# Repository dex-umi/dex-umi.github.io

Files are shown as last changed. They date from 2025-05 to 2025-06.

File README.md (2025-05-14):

# Academic Project Page Template
This is an academic paper project page template.

Example project pages built using this template are:
- https://horwitz.ai/probex
- https://vision.huji.ac.il/probegen
- https://horwitz.ai/mother
- https://horwitz.ai/spectral_detuning
- https://vision.huji.ac.il/ladeda
- https://vision.huji.ac.il/dsire
- https://horwitz.ai/podd
- https://dreamix-video-editing.github.io
- https://horwitz.ai/conffusion
- https://horwitz.ai/3d_ads/
- https://vision.huji.ac.il/ssrl_ad
- https://vision.huji.ac.il/deepsim

## Start using the template
To start using the template click on `Use this Template`.

The template uses html for controlling the content and css for controlling the style. 
To edit the websites contents edit the `index.html` file. It contains different HTML "building blocks", use whichever ones you need and comment out the rest.  

**IMPORTANT!** Make sure to replace the `favicon.ico` under `static/images/` with one of your own, otherwise your favicon is going to be a dreambooth image of me.

## Components
- Teaser video
- Images Carousel
- Youtube embedding
- Video Carousel
- PDF Poster
- Bibtex citation

## Tips:
- The `index.html` file contains comments instructing you what to replace, you should follow these comments.
- The `meta` tags in the `index.html` file are used to provide metadata about your paper 
(e.g. helping search engine index the website, showing a preview image when sharing the website, etc.)
- The resolution of images and videos can usually be around 1920-2048, there rarely a need for better resolution that take longer to load. 
- All the images and videos you use should be compressed to allow for fast loading of the website (and thus better indexing by search engines). For images, you can use [TinyPNG](https://tinypng.com), for videos you can need to find the tradeoff between size and quality.
- When using large video files (larger than 10MB), it's better to use youtube for hosting the video as serving the video from the website can take time.
- Using a tracker can help you analyze the traffic and see where users came from. [statcounter](https://statcounter.com) is a free, easy to use tracker that takes under 5 minutes to set up. 
- This project page can also be made into a github pages website.
- Replace the favicon to one of your choosing (the default one is of the Hebrew University). 
- Suggestions, improvements and comments are welcome, simply open an issue or contact me. You can find my contact information at [https://horwitz.ai](https://horwitz.ai)

## Acknowledgments
Parts of this project page were adopted from the [Nerfies](https://nerfies.github.io/) page.

## Website License
<br />This work is licensed under a <a rel="license" href="http://creativecommons.org/licenses/by-sa/4.0/">Creative Commons Attribution-ShareAlike 4.0 International License</a>.

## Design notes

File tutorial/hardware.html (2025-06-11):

Back to Main Page

# DexUMI Hardware Assembly Tutorial

## Step-by-step guide for building your DexUMI exoskeleton

## Exoskeleton Model Preview

Explore the CAD views of both XHand and Inspire Hand DexUMI

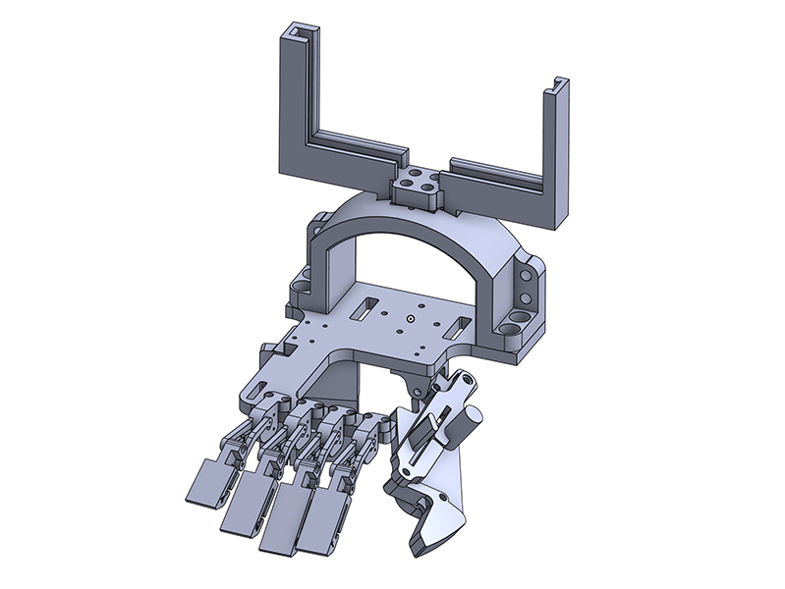
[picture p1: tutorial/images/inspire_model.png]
Inspire Hand DexUMI Model Preview
 (https://cad.onshape.com/documents/7e158032a91b5681734a0bac/w/ddb7f35eb14f420c872ab185/e/6841f3fc3ef2e646e71b0ba4)

Inspire Hand DexUMI Model

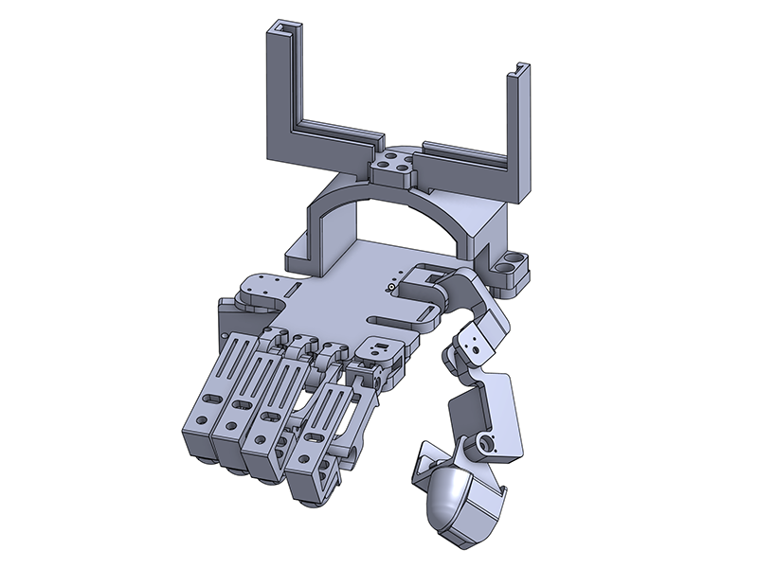
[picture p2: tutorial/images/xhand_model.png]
XHand DexUMI Model Preview
 (https://cad.onshape.com/documents/e4e375a7acd566624676e79d/w/0ad885893abcd26f135bcb35/e/56bcc60d6cd295dfe515c23f)

XHand DexUMI Model

Click on a model to view it directly in Onshape. You can also export the model in various 3D formats supported by Onshape.

- Download Formats: STL, STEP, SolidWorks, and more
- Printer: Bambu X1C
- Material: PLA-CF
- Print Settings: 50% sparse infill density, 50% infill/wall overlap, 10 wall loops

Download DexUMI_Inspire.3mf Download DexUMI_XHand.3mf

Feel free to tweak the settings based on your printer and material availability!

## PCB Sourcing

Information for sourcing and fabricating DexUMI circuit boards

Download Schematics Download Gerber Files Download Pick and Place Download BOM

### Step-by-step Tutorial of Ordering PCBA

To get started, you’ll first need to order the DexUMI circuit board. In this tutorial, we use JLCPCB as the PCB manufacturer.
On the JLCPCB homepage (https://jlcpcb.com/), click the Order Now button and follow the step-by-step guide in the image tutorial below.

First, upload the Gerber file we provided (click the download button above to get it).

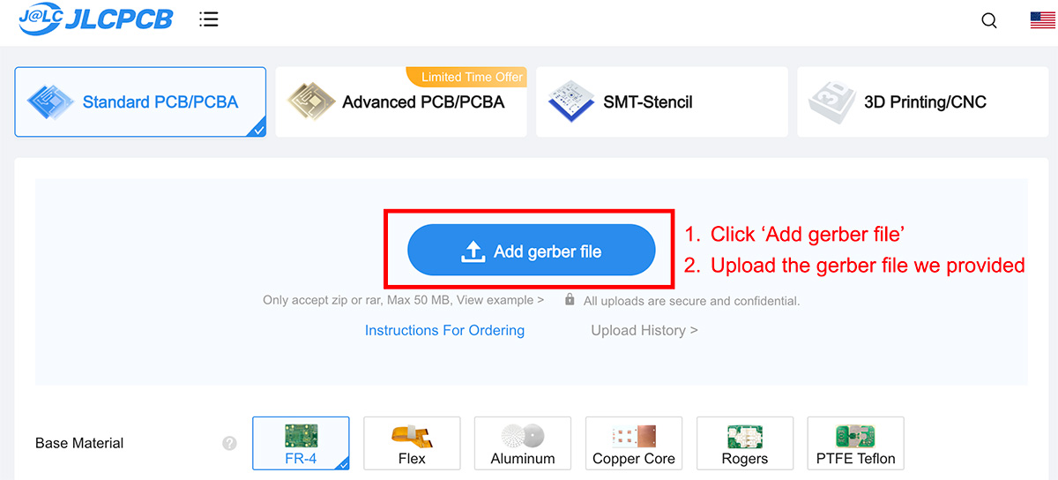
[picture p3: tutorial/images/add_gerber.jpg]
Add Gerber File


Second, follow the image tutorial below to select the correct manufacturer parameters.

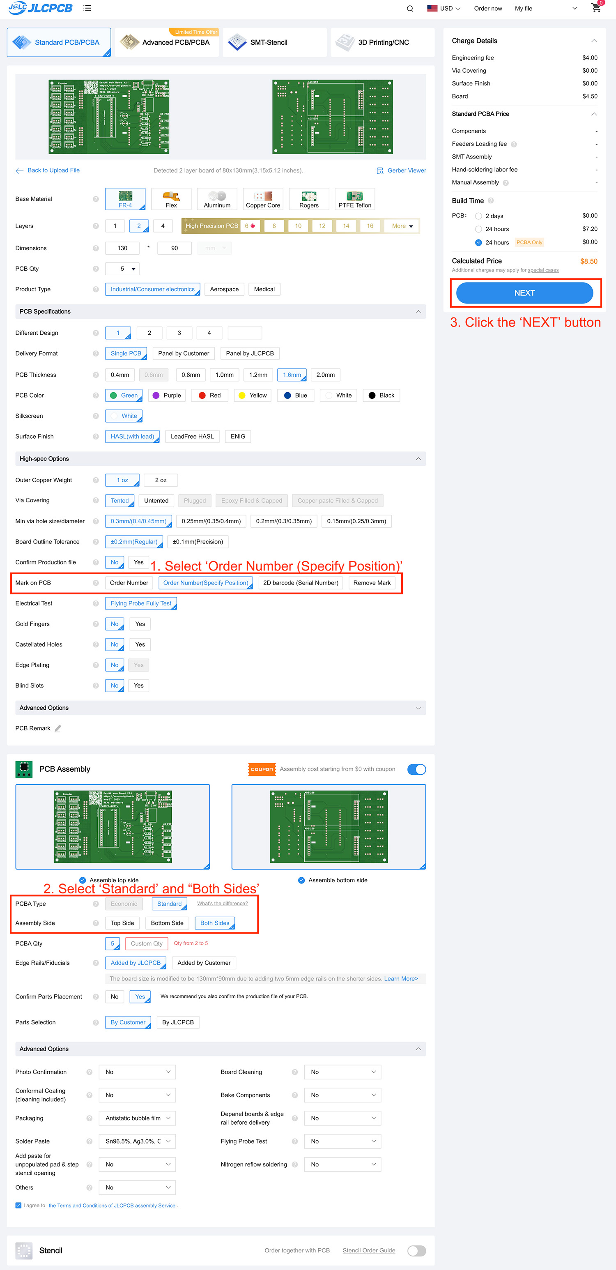
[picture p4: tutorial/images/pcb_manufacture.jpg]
PCB Manufacture Settings


On the new page, click the Bill of Materials column, then upload the BOM file and Pick and Place file we provided.

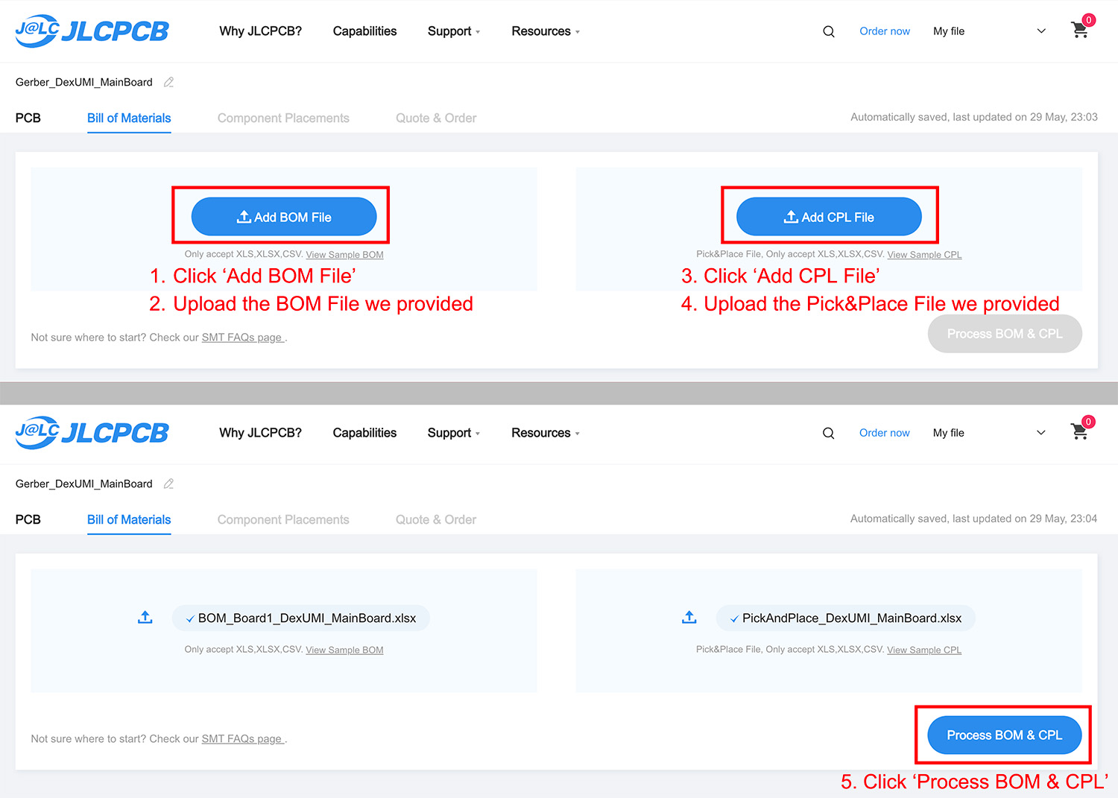
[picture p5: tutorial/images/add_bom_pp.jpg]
Add BOM and Pick and Place


After processing, you’ll be presented with a parts confirmation list. If everything is in stock, simply click the NEXT button. If not, you’ll need to manually select similar parts using the suggestions provided by the ordering system.

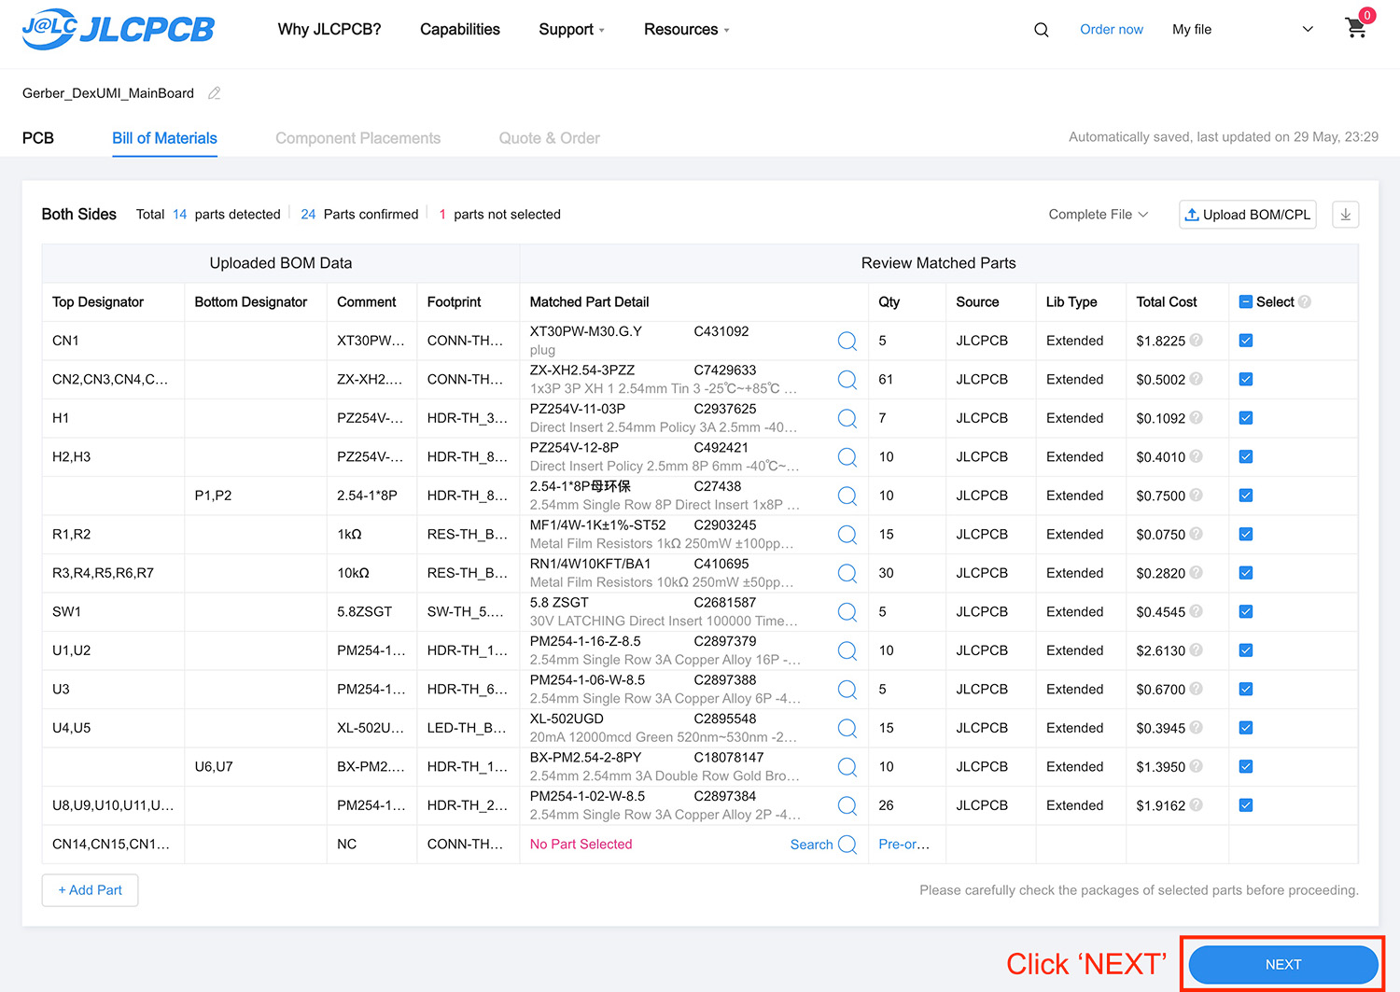
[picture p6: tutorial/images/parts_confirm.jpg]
Parts Confirmation


The system may display a message like Project has unselected parts. Don’t worry — this happens because we include some NC (Not Connected) parts, which are not meant to be assembled. Simply click the Do not place button to proceed.

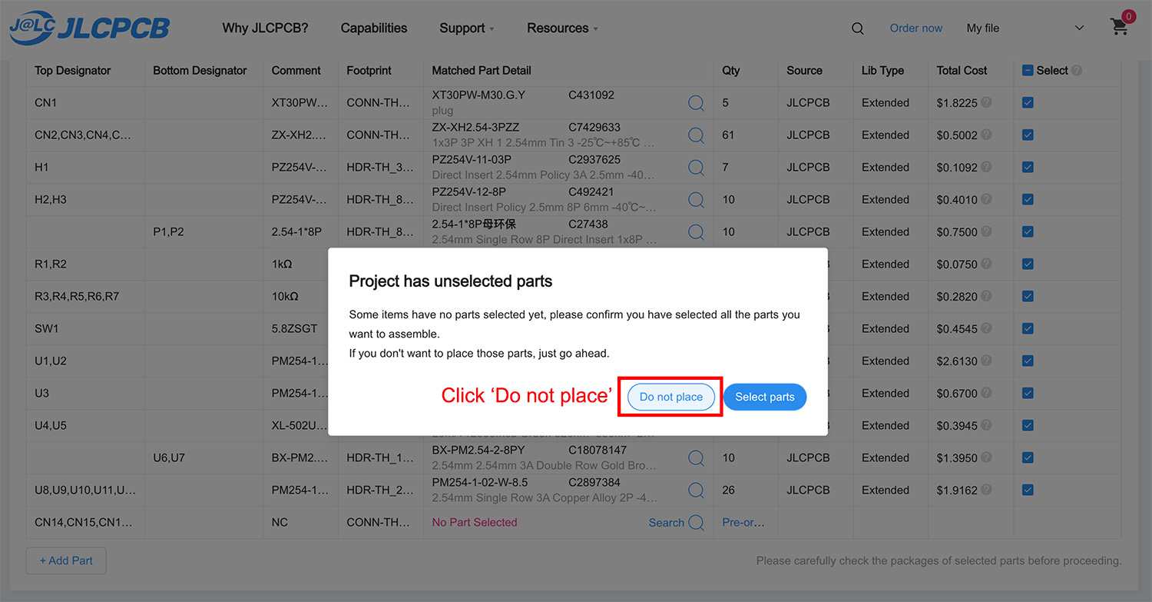
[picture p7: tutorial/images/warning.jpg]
Unselected Parts Warning


🎉 Hurray! The last step! You can now preview the 3D model of your circuit board. If all parts are rendered correctly and look similar to the images below, go ahead and click the NEXT button to place the order!

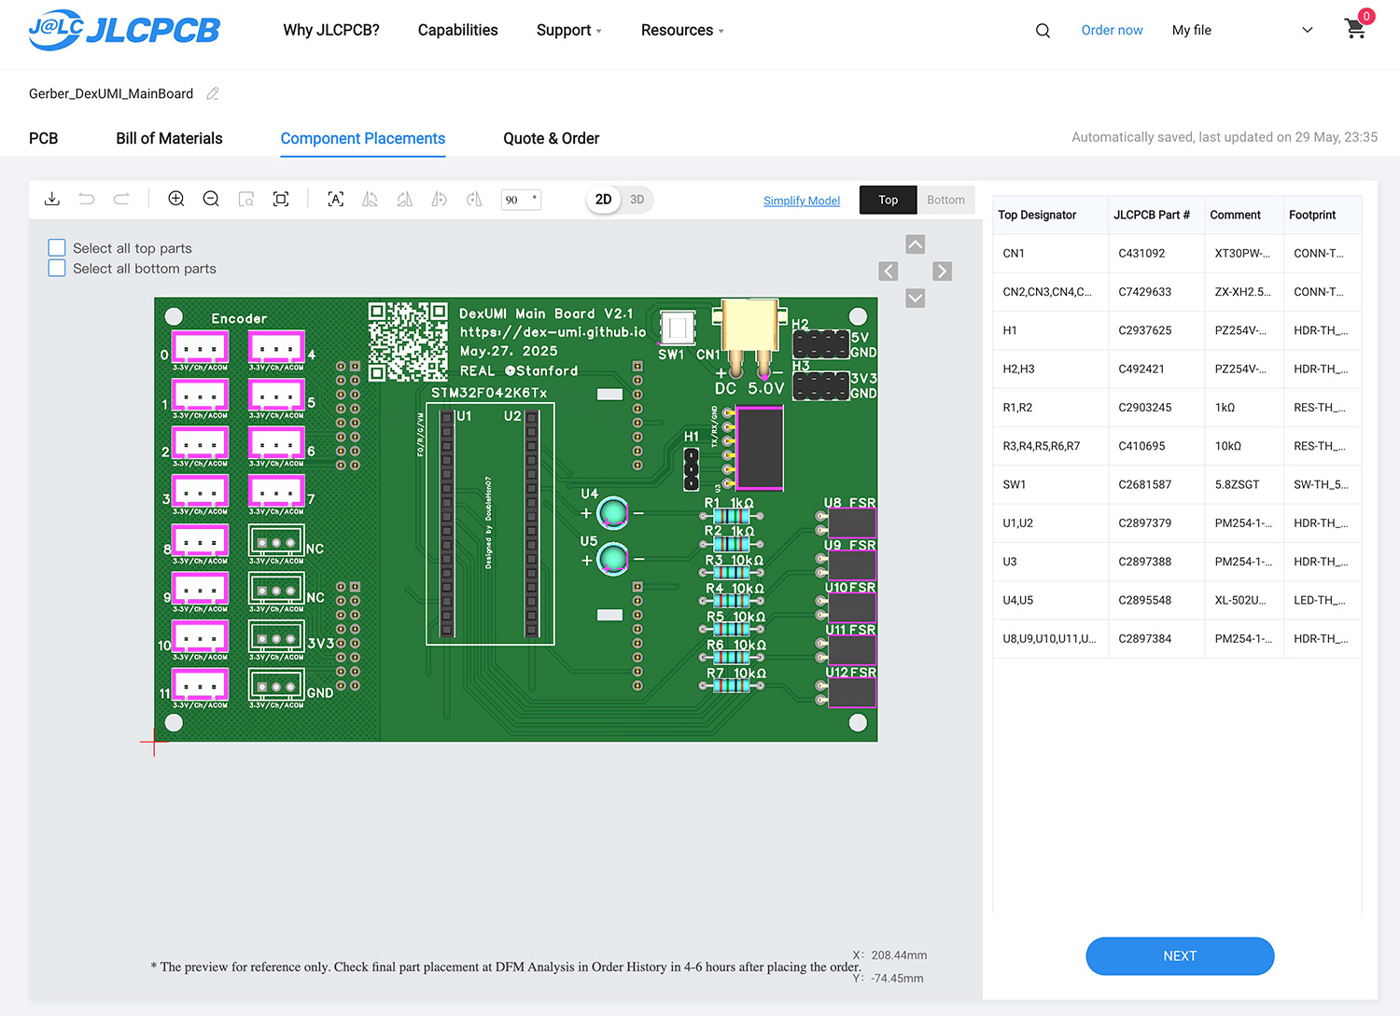
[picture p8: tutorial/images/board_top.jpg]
Board Top View


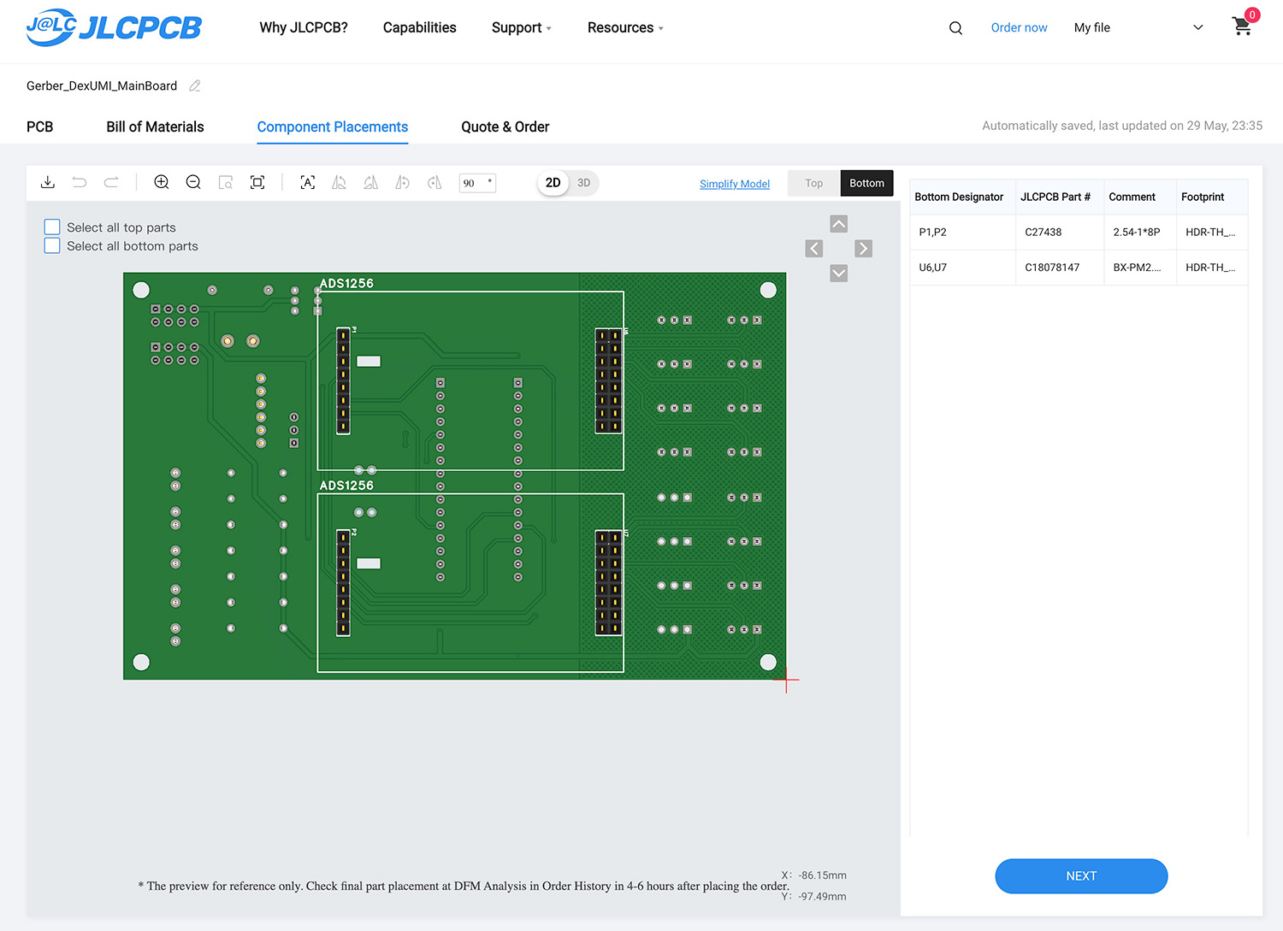
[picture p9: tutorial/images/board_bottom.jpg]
Board Bottom View


## Structural Bill of Materials (BOM)

All structural parts needed to build Inspire Hand and XHand DexUMI

This is a compact summary of all hardware components required. Tables are grouped by device and category. Click the links to purchase directly.

### Inspire Hand DexUMI

Part | Qty | Price
Materials
Bambu PLA-CF Matcha Green (https://us.store.bambulab.com/products/pla-cf?id=41158283591816) | 400g | $34.99 (1kg)
Electronics
XH 2.54mm-3P Wire 50cm (https://www.amazon.com/Kidisoii-2-54mm-Housing-Pre-Crimped-Adapter/dp/B0BW69ZB3M/) | 6 | $7.65 (5pcs)
RDC506018A Encoder: DigiKey (https://www.digikey.com/en/products/detail/alps-alpine/RDC506018A/19529120), Mouser (https://www.mouser.com/ProductDetail/Alps-Alpine/RDC506018A?qs=j%252B1pi9TdxUZl0Obrq5eEAQ%3D%3D) | 6 | $1.66 (1pc)
Fasteners
M1x8mm Screws (https://www.amazon.com/dp/B0C1SBGGY6/) | 4 | $7.99 (100pcs)
M1 Hex Nuts (https://www.mcmaster.com/90591A311/) | 4 | $4.47 (10pcs)
M2 Screws (6/12/16mm) (https://www.amazon.com/Kadrick-Assortment-Button-Stainless-Washers/dp/B0BX96SMW4/) | 8+1+2 | $8.99 (660pcs kit)
M2 Lock Nuts (https://www.amazon.com/binifiMux-100pcs-Stainless-Nylock-Locking/dp/B07L2W3QX3/) | 11 | $9.99 (100pcs)
M3 Lock Nuts (https://www.amazon.com/M3-Locknuts-Self-Lock-Stainless-Self/dp/B0D146SHYF/) | 4 | $5.99 (120pcs)
D-shape Screws
M3 Shoulder Screws 8mm (https://www.mcmaster.com/90265A119/) | 4 | $5.29 (1pc)
M3 Shoulder Screws 15mm (https://www.mcmaster.com/90265A182/) | 1 | $4.33 (1pc)
M3 Shoulder Screws 25mm (https://www.mcmaster.com/90265A874/) | 1 | $4.94 (1pc)
Accessories
Finger Sleeves (https://www.amazon.com/ELANE-Holster-Support-Elastic-basketball/dp/B08RYPTS54/) | 10 | $9.97 (40pcs)
3M TB641 Gripping Material (https://www.amazon.com/gp/product/B0093CQPW8/) | 1.5ft | $54.14 (15 ft)
iPhone Mounting
M3x16mm Screws + M3 Hex Nuts (https://www.amazon.com/Screws-Assortment-Plated-Socket-Washers/dp/B0D3X5CT2J/) | 4+4 | $8.99 (600pcs kit)
M6x20mm Screws + M6 Hex Nuts (https://www.amazon.com/Screws-Assortment-Stainless-Socket-Washers/dp/B0DFWMGFDM/) | 4+4 | $8.99 (172pcs kit)
Camera System
OAK-1 W (https://shop.luxonis.com/products/oak-1-w?variant=44051403604191) | 1 | $249 (1pc)
M4x6mm Screws (https://www.amazon.com/Kadrick-Assortment-Stainless-Washers-Wrenche/dp/B0BZ6Y8KRD/) | 2 | $9.99 (300pcs kit)
USB-C to USB-A (10ft) (https://www.amazon.com/Anker-Powerline-Pull-up-Resistor-MacBook/dp/B01MZIPYPY) | 1 | $16.99 (1pc)
Consumables
Loctite Threadlocker 242 (https://www.amazon.com/Loctite-Heavy-Duty-Threadlocker-Single/dp/B000I1RSNS/) | 0.03 fl oz | $5.98 (0.2 fl oz)
UV Resin (https://www.amazon.com/dp/B0BJ65T85R/) | 20g | $11.99 (30g)
Super Glue (https://www.amazon.com/Scotch-Super-Liquid-Ounces-AD114/dp/B001PILFVY/) | 1pc | $6.98 (4pcs)
Lubricate Grease (https://www.amazon.com/Lucas-Oil-10533-Lithium-Grease/dp/B004X70LZA/) | 0.2oz | $5.98 (8oz)

### XHand DexUMI

Part | Qty | Price
Materials
Bambu PLA-CF Matcha Green (https://us.store.bambulab.com/products/pla-cf?id=41158283591816) | 600g | $34.99 (1kg)
Electronics
XH 2.54mm-3P Wire 50cm (https://www.amazon.com/Kidisoii-2-54mm-Housing-Pre-Crimped-Adapter/dp/B0BW69ZB3M/) | 12 | $7.65 (5pcs)
RDC506018A Encoder: DigiKey (https://www.digikey.com/en/products/detail/alps-alpine/RDC506018A/19529120), Mouser (https://www.mouser.com/ProductDetail/Alps-Alpine/RDC506018A?qs=j%252B1pi9TdxUZl0Obrq5eEAQ%3D%3D) | 12 | $1.66 (1pc)
Fasteners
M2 Screws (12/16mm), M2 Hex Nuts (https://www.amazon.com/Kadrick-Assortment-Button-Stainless-Washers/dp/B0BX96SMW4/) | 7+6+8 | $8.99 (660pcs kit)
M2 Lock Nuts (https://www.amazon.com/binifiMux-100pcs-Stainless-Nylock-Locking/dp/B07L2W3QX3/) | 5 | $9.99 (100pcs)
M3 Hex Nuts (https://www.amazon.com/Screws-Assortment-Plated-Socket-Washers/dp/B0D3X5CT2J/) | 7 | $8.99 (600pcs kit)
M3 Lock Nuts (https://www.amazon.com/M3-Locknuts-Self-Lock-Stainless-Self/dp/B0D146SHYF/) | 7 | $5.99 (120pcs)
D-shape Screws
M3 Shoulder Screws 10mm (https://www.mcmaster.com/90265A121) | 9 | $3.12 (1pc)
M3 Shoulder Screws 20mm (https://www.mcmaster.com/90265A124) | 3 | $5.65 (1pc)
Accessories
Cable Ties (https://www.amazon.com/Reusable-Newlan-Adjustable-Organizer-Management/dp/B081HH5X61/) | 5 | $6.28 (60pcs)
3M TB641 Gripping Material (https://www.amazon.com/gp/product/B0093CQPW8/) | 1.5ft | $54.14 (15 ft)
iPhone Mounting
M3x16mm Screws + M3 Hex Nuts (https://www.amazon.com/Screws-Assortment-Plated-Socket-Washers/dp/B0D3X5CT2J/) | 4+4 | same as above
M6x20mm Screws + M6 Hex Nuts (https://www.amazon.com/Screws-Assortment-Stainless-Socket-Washers/dp/B0DFWMGFDM/) | 4+4 | $8.99 (172pcs kit)
Camera System
OAK-1 W (https://shop.luxonis.com/products/oak-1-w?variant=44051403604191) | 1 | $249 (1pc)
M4x6mm Screws (https://www.amazon.com/Kadrick-Assortment-Stainless-Washers-Wrenche/dp/B0BZ6Y8KRD/) | 2 | $9.99 (300pcs kit)
USB-C to USB-A (10ft) (https://www.amazon.com/Anker-Powerline-Pull-up-Resistor-MacBook/dp/B01MZIPYPY) | 1 | $16.99 (1pc)
Consumables
Loctite Threadlocker 242 (https://www.amazon.com/Loctite-Heavy-Duty-Threadlocker-Single/dp/B000I1RSNS/) | 0.02 fl oz | $5.98 (0.2 fl oz)
UV Resin (https://www.amazon.com/dp/B0BJ65T85R/) | 20g | $11.99 (30g)
Super Glue (https://www.amazon.com/Scotch-Super-Liquid-Ounces-AD114/dp/B001PILFVY/) | 1pc | $6.98 (4pcs)
Lubricate Grease (https://www.amazon.com/Lucas-Oil-10533-Lithium-Grease/dp/B004X70LZA/) | 0.2oz | $5.98 (8oz)

## Electronics Bill of Materials (BOM)

All electronic components and modules for DexUMI circuits

This is a compact summary of all hardware components required. Tables are grouped by device and category. Click the links to purchase directly.

### Electronic Modules

Part | Qty | Price
Modules
STM32F042K6T6 Core Board (https://www.aliexpress.com/i/2255800720094040.html) | 1 | $15.39 (1pc)
ADS1256 Module (https://www.aliexpress.us/item/3256806212460099.html) | 2 | $15.44 (1pc)
USB to TTL Module (https://www.amazon.com/JESSINIE-Module-CH343-Communication-Microcontroller/dp/B0D6352BS9/) | 1 | $9.95 (3pcs)
ST-Link V2 Downloader (https://www.amazon.com/AITRIP-Emulator-Downloader-Programmer-STM32F103C8T6/dp/B0D22S8WVX/) | 1 | $5.99 (1pc)
Accessories
DC Power Supply (https://www.amazon.com/ALIENTEK-Adjustable-DP100-Precision-Regulated/dp/B0CRDJBPRV/) | 1 | $60.15 (1pc)
XT30 Female Connectors w/ Wire (https://www.amazon.com/BDHI-Female-Connectors-Turnigy-BDHI-19/dp/B08FRBJL1C/) | 1 | $8.58 (5pcs)
Dupont Cable Male to Female (https://www.amazon.com/EDGELEC-Breadboard-1pin-1pin-Connector-Multicolored/dp/B07GD2BWPY/) | 3 | $6.98 (120pcs assorted)
Automotive Cloth Tape (https://www.amazon.com/Radio-Wiring-Harness-Cloth-Tape/dp/B08RS5P3WZ/) | 1 rolls | $9.99 (2pcs)

## Prepare Common Components

Essential components needed for both exoskeleton

#### Items

- D-screw components (screws, nuts, and tools)
- Encoder cable materials
- Encoder module parts

#### Make D-Screw

#### Prepare Encoder Cable

#### Build Encoder Module

## XHand Exoskeleton Assembly Guide

#### XHand Index Assembly Guide

#### XHand Middle/Ring/Pinky Assembly Guide

#### Xhand Thumb Assembly Guide

#### Assemble Fingers to the Palm

#### Oak Camera Mounting

#### Connect XHand Exoskeleton to the DexUMI Circuit Board

Follow the wiring sequence shown in the image below to connect encoders to the circuit board.

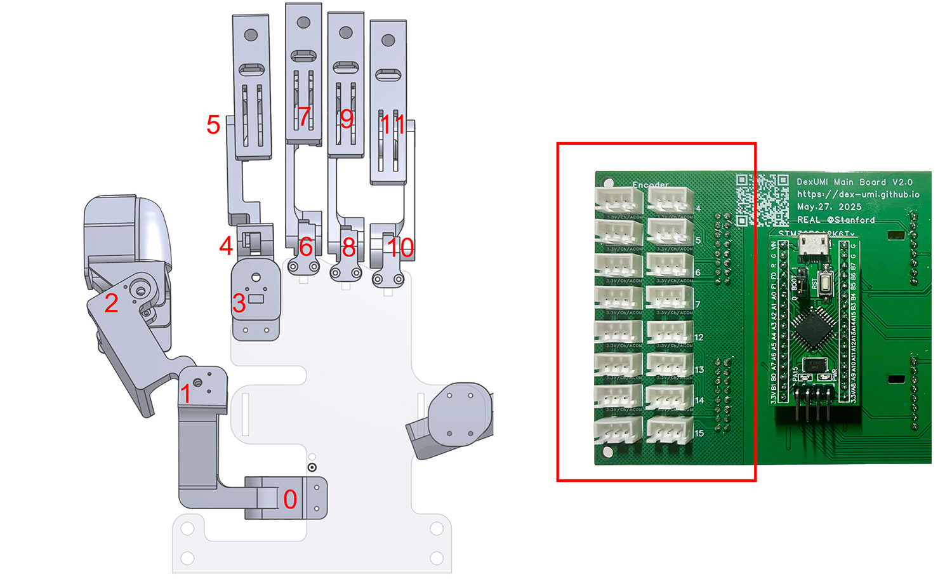
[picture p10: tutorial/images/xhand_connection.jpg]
XHand Connection Diagram


## Inspire Hand Exoskeleton Assembly

#### Inspire Index/Middle/Ring/Pinky Assembly Guide

#### Inspire Thumb Assembly Guide

#### Step 3: Oak Camera Mounting

#### Connect Inspire Hand Exoskeleton to the DexUMI Circuit Board

Follow the wiring sequence shown in the image below to connect encoders to the circuit board.

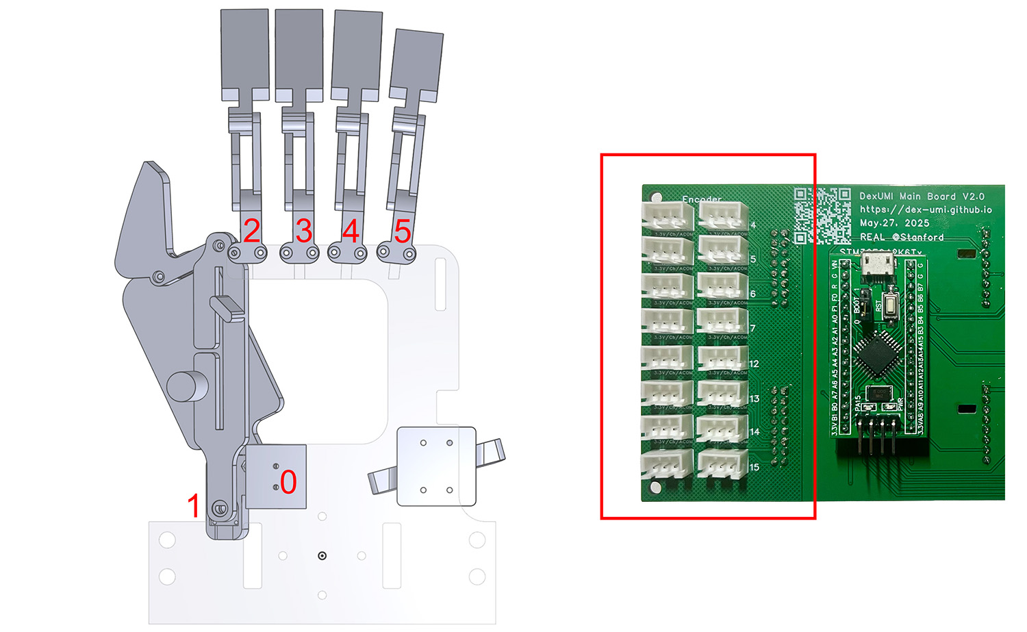
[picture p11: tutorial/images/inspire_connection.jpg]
Inspire Hand Connection Diagram


## Share Steps

Steps needed for both exoskeleton

#### iPhone Mounting

#### Finger Grip Tape

#### Flash the Firmware to DexUMI MCU

DexUMI Inspire Firmware (https://github.com/real-stanford/DexUMI/blob/main/embedded_system/assets/DexUMI_Inspire.hex) DexUMI XHand Firmware (https://github.com/real-stanford/DexUMI/blob/main/embedded_system/assets/DexUMI_XHand.hex)

To flash the firmware into the MCU, we first need to install openocd (https://openocd.org/pages/getting-openocd.html) on the target PC:

sudo apt-get install openocd

Then connect the MCU with ST-LINK V2, as shown below:

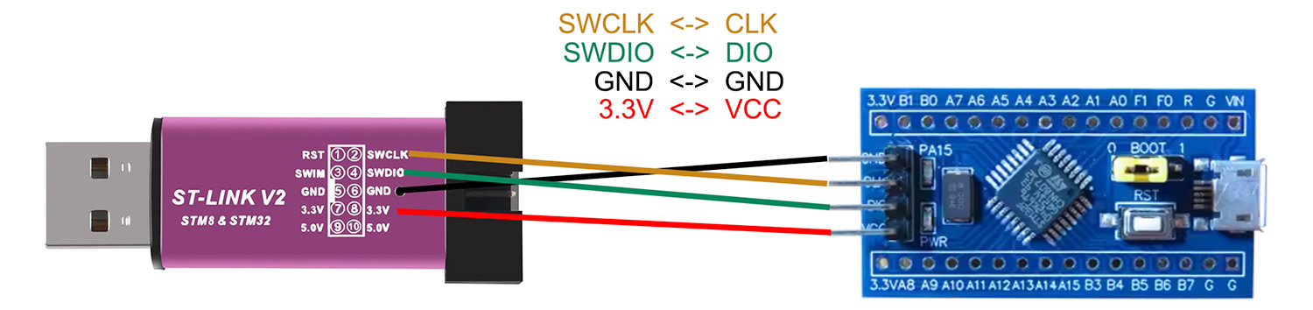
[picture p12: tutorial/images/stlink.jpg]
ST-LINK Connection Diagram


Finally, run this script to flash the firmware into the MCU.

For Inspire Hand DexUMI:

openocd -f interface/stlink-v2.cfg -f target/stm32f0x.cfg -c "program DexUMI_Inspire.hex verify reset exit"

For XHand DexUMI:

openocd -f interface/stlink-v2.cfg -f target/stm32f0x.cfg -c "program DexUMI_XHand.hex verify reset exit"

#### Connect the DexUMI Circuit Board to Your PC

First, we need to install the MCU board and ADC modules on the DexUMI circuit board.

Insert the MCU at the top of the board, as shown below:

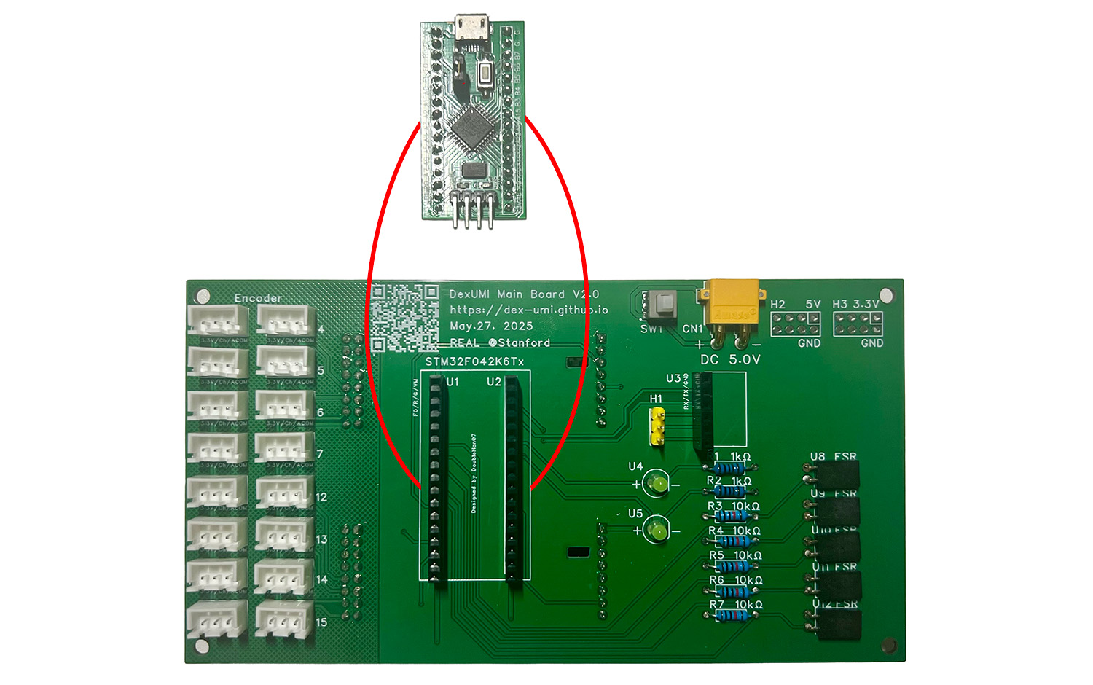
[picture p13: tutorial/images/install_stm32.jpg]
Install STM32 MCU


Then insert the ADC modules at the bottom of the board:

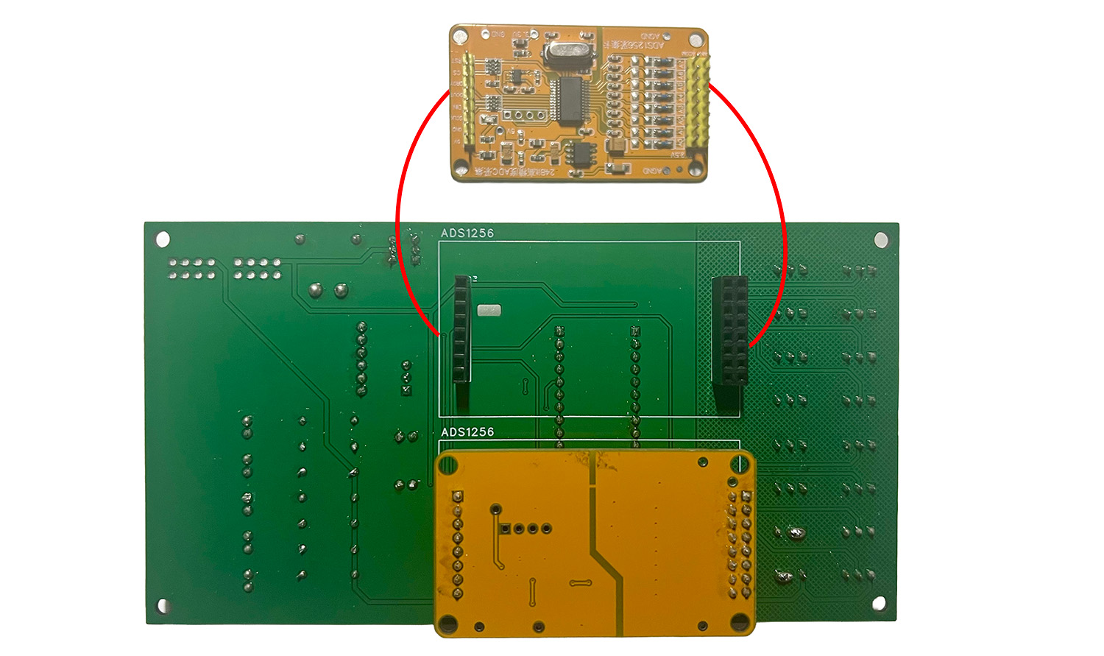
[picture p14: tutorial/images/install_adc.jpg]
Install ADC Modules


Next, power on the board. Connect DC 5.0V 1.0A through the XT30 female connector using a wired input, then press the switch to power up.

Finally, connect the board to your PC using a USB-TTL module, as shown below:

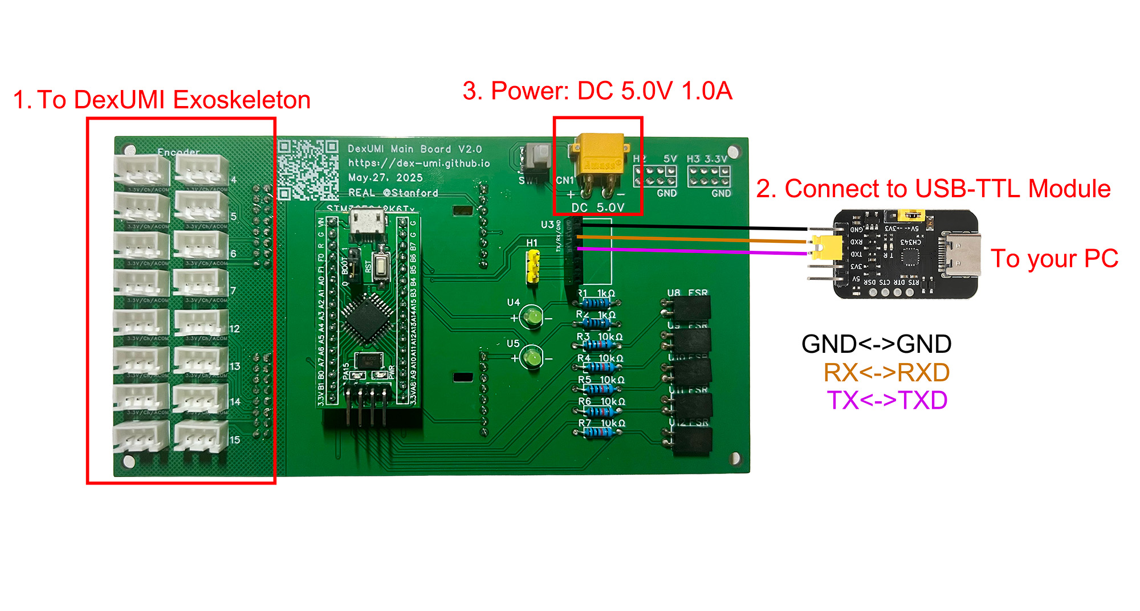
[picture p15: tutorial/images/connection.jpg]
Connect with USB-TTL


This page was built using the Academic Project Page Template (https://github.com/eliahuhorwitz/Academic-project-page-template) which was adopted from the Nerfies (https://nerfies.github.io) project page. This website is licensed under a Creative Commons Attribution-ShareAlike 4.0 International License (http://creativecommons.org/licenses/by-sa/4.0/).

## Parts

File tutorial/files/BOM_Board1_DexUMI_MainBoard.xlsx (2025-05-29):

No. | Quantity | Comment | Designator | Footprint | Value | Manufacturer Part | Manufacturer | Supplier Part | Supplier
1 | 1 | XT30PW-M30.G.Y | CN1 | CONN-TH_XT30PW-M |  | XT30PW-M30.G.Y | AMASS(艾迈斯) | C431092 | LCSC
2 | 12 | ZX-XH2.54-3PZZ | CN2,CN3,CN4,CN5,CN6,CN7,CN8,CN9,CN10,CN11,CN12,CN13 | CONN-TH_3P-P2.54_2501S-3P |  | ZX-XH2.54-3PZZ | Megastar(兆星) | C7429633 | LCSC
3 | 4 | NC | CN14,CN15,CN16,CN17 | CONN-TH_3P-P2.54_2501S-3P |  | NC | Megastar(兆星) | C7429633 | LCSC
4 | 1 | PZ254V-11-03P | H1 | HDR-TH_3P-P2.54-V-M |  | PZ254V-11-03P | XFCN(兴飞) | C2937625 | LCSC
5 | 2 | PZ254V-12-8P | H2,H3 | HDR-TH_8P-P2.54-V-M-R2-C4-S2.54 |  | PZ254V-12-8P | XFCN(兴飞) | C492421 | LCSC
6 | 2 | 2.54-1*8P | P1,P2 | HDR-TH_8P-P2.54-V-F-1 |  | 2.54-1*8P | BOOMELE(博穆精密) | C27438 | LCSC
7 | 2 | 1kΩ | R1,R2 | RES-TH_BD2.7-L6.2-P10.20-D0.4 | 1kΩ | MF1/4W-1K±1%-ST52 | VO(翔胜) | C2903245 | LCSC
8 | 5 | 10kΩ | R3,R4,R5,R6,R7 | RES-TH_BD2.4-L6.3-P10.30-D0.6 | 10kΩ | RN1/4W10KFT/BA1 | Tyohm(幸亚电阻) | C410695 | LCSC
9 | 1 | 5.8 ZSGT | SW1 | SW-TH_5.8ZSGT |  | 5.8 ZSGT | SHOU HAN(首韩) | C2681587 | LCSC
10 | 2 | PM254-1-16-Z-8.5 | U1,U2 | HDR-TH_16P-P2.54-V-F-A |  | PM254-1-16-Z-8.5 | HCTL(华灿天禄) | C2897379 | LCSC
11 | 1 | PM254-1-06-W-8.5 | U3 | HDR-TH_6P-P2.54-H-F-W10.0-N |  | PM254-1-06-W-8.5 | HCTL(华灿天禄) | C2897388 | LCSC
12 | 2 | XL-502UGD | U4,U5 | LED-TH_BD5.9-P2.54-RD_GREEN |  | XL-502UGD | XINGLIGHT(成兴光) | C2895548 | LCSC
13 | 2 | BX-PM2.54-2-8PY | U6,U7 | HDR-TH_16P-P2.54-V-F-R2-C8-S2.54-1 |  | BX-PM2.54-2-8PY | Bossie(博锡) | C18078147 | LCSC
14 | 5 | PM254-1-02-W-8.5 | U8,U9,U10,U11,U12 | HDR-TH_2P-P2.54-H-F-W10.0-N |  | PM254-1-02-W-8.5 | HCTL(华灿天禄) | C2897384 | LCSC

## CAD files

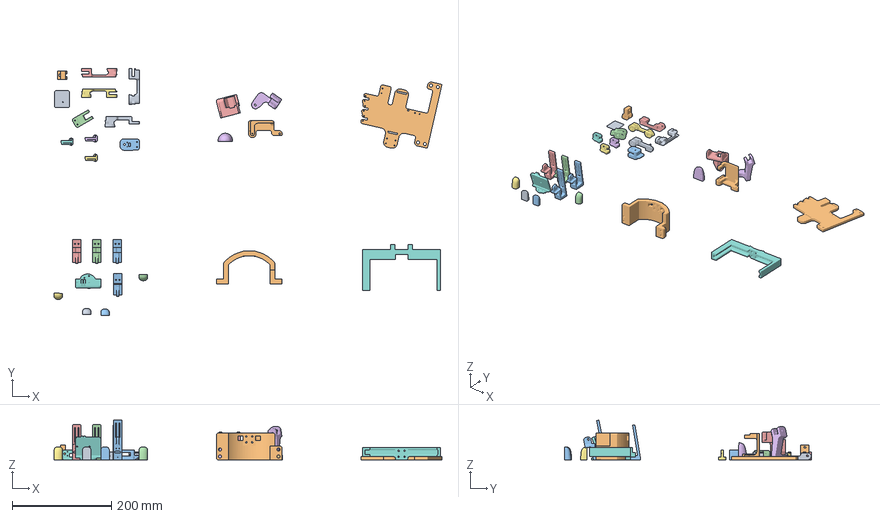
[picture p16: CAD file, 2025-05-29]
tutorial/files/DexUMI_XHand.3mf
782.5 x 497.2 x 80.5 mm
xhand_exo_v3 - pinky_finger-1 xhand_right_rot-1.STL
xhand_exo_v3 - palm_connector.STL
xhand_exo_v3 - index_finger_thin-1 xhand_tip_tactile_wo_shell-1.STL
xhand_exo_v3 - middle_finger-1 xhand_tip_tactile_wo_shell-2.STL
xhand_exo_v3 - ring_finger-1 xhand_tip_tactile_wo_shell.STL
xhand_exo_v3 - thumb_finger-1 thumb_tactile_new-1.STL
xhand_exo_v3 - ring_finger-1 index_tactile_new-1.STL
xhand_exo_v3 - oak_xhand-1.STL
xhand_exo_v3 - middle_finger-1 index_tactile_new-1.STL
xhand_exo_v3 - xhand_palm-1.STL
xhand_exo_v3 - index_finger_thin-1 index_tactile_new-1.STL
xhand_exo_v3 - pinky_finger-1 index_tactile_new-1.STL
xhand_exo_v3 - ring_finger-1 xhand_left_rot-1.STL
xhand_exo_v3 - xhand_thumb_split-1.STL
xhand_exo_v3 - middle_finger-1 xhand_left_rot-2.STL
xhand_exo_v3 - iphone_15_pro_mounting-1.STL
xhand_exo_v3 - index_finger_thin-1 xhand_index_rot-2.STL
xhand_exo_v3 - thumb_finger-1 xhand_thumb_rot-1.STL
xhand_exo_v3 - xhand_index_link-1.STL
xhand_exo_v3 - xhand_thumb_link-2.STL
xhand_exo_v3 - thumb_finger-1 xhand_thumb_tip_tactile-1.STL
xhand_exo_v3 - xhand_finger_link-1.STL
xhand_exo_v3 - xhand_finger_link-2.STL
xhand_exo_v3 - xhand_finger_link-3.STL
xhand_exo_v3 - thumb_padding-1.STL
xhand_exo_v3 - xhand_index_split-1.STL
xhand_exo_v3 - pinky_finger-1 xhand_tip_tactile_wo_shell_pinky-1.STL

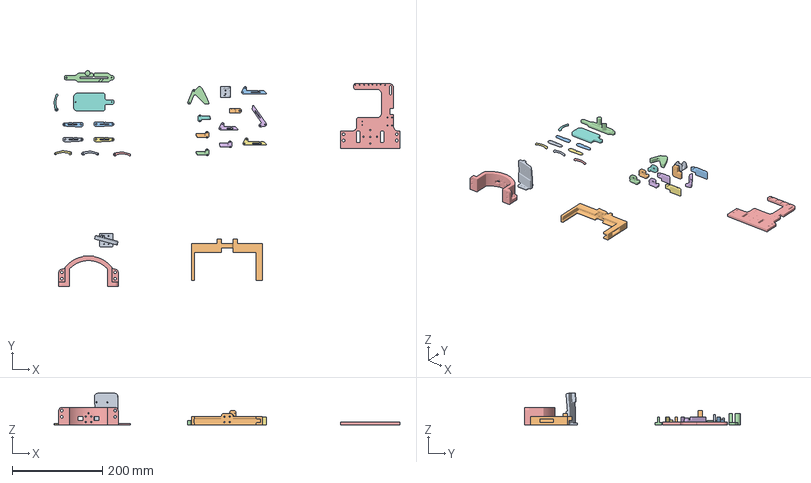
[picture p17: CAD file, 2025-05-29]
tutorial/files/DexUMI_Inspire.3mf
766.7 x 477.9 x 70.9 mm
exo_v6 - oak_inspire_new_exo-1.STL
exo_v6 - iphone_15_pro_mounting-1.STL
exo_v6 - middle_linkage4-1.STL
exo_v6 - thumb_linkage2-1.STL
exo_v6 - palm_connector-1.STL
exo_v6 - index_linkage4-1.STL
exo_v6 - ring_linkage4-1.STL
exo_v6 - thumb_linkage4-1.STL
exo_v6 - thumb_link-2.STL
exo_v6 - thumb_linkage1-2.STL
exo_v6 - linkage1-2.STL
exo_v6 - thumb_linkage3-1.STL
exo_v6 - palm-1.STL
exo_v6 - pinky_linkage4-1.STL
exo_v6 - linkage1-3.STL
exo_v6 - finger_link-3.STL
exo_v6 - linkage1-1.STL
exo_v6 - finger_link-4.STL
exo_v6 - linkage1-4.STL
exo_v6 - finger_link-2.STL
exo_v6 - linkage3-2.STL
exo_v6 - finger_link-1.STL
exo_v6 - linkage3-3.STL
exo_v6 - linkage3-4.STL
exo_v6 - linkage3-1.STL

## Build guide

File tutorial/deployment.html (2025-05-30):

Back to Main Page

# DexUMI Deployment Guide

## Deploy DexUMI in real-world

## Installation

Mamba Env and external dependency

Tested on Ubuntu 22.04 with both NVIDIA L40S and RTX 4090 GPU. We recommend using GPU with larger memory such that you can process longer demonstration.

#### Environment Setup

Terminal - Environment Setup

# We recommend Miniforge for faster installation
cd DexUMI
mamba env create -f environment.yml
mamba activate dexumi
# optional: to set the DEV_PATH in your bashrc or zshrc
export DEV_PATH="/parent/directory/of/DexUMI"

DexUMI utilizes SAM2 (https://github.com/facebookresearch/sam2) and ProPainter (https://github.com/sczhou/ProPainter) to track and remove the exoskeleton and hand. Our system uses Record3D (https://github.com/marek-simonik/record3d) to track the wrist pose. To make Record3D compatible with Python 3.10, please follow the instructions here (https://github.com/marek-simonik/record3d/issues/89). Alternatively, you can directly install our forked version (https://github.com/mengdaxu/record3d), which already integrates the solution.

Please clone the above three packages into the same directory as DexUMI. The final folder structure should be:

.
├── DexUMI
├── sam2
├── ProPainter
├── record3D

Download the SAM2 checkpoint sam2.1_hiera_large.pt into sam2/checkpoints/ and install SAM2.

Terminal - Environment Setup

cd sam2
pip install -e .

You also need to install Record3D on your iPhone. We use iPhone 15 Pro Max to track the wrist pose. You can use any iPhone model with ARKit capability, but you might need to modify some CAD models to adapt to other iPhone dimensions.

## Fitting Encoder to Motor Regression

Build action mapping between exoskeleton and robot hardware

The goal is to fit a regression model that maps the joint encoder readings from the exoskeleton to the motor value on the robot hand such that the fingertips of the exoskeleton can perfectly overlayed with the fingertips of the robot hand on the wrist camera image space. We achive this by uniformly sampling the robot hand motor value between lower limit and upper limit. Human manully rotates the exoskeleton joint to align the fingertips in the wrist camera image. We can repeat this process to get a pair data point (encoder reading, motor value). After collecting enough data points, we can fit a linear regression model to map the encoder reading to the motor value. We follow the steps below to fit the model:

# Pseudocode for Motor-Encoder Regression Data Collection
for motor_id in robot_hand_motors:
motor_values = []
encoder_readings = []

for motor_value in uniform_sample(motor_lower_limit, motor_upper_limit):
# 1) Send sampled motor value to robot hand
robot_hand.send_motor_command(motor_id, motor_value)

# 2) Robot hand executes the command
robot_hand.execute_command()
wait_for_completion()

# 3) Manually rotate corresponding exoskeleton joint
# to overlay fingertips in wrist camera image
Human("Align exoskeleton fingertip with robot fingertip")

# 4) Record the encoder reading
encoder_value = exoskeleton.read_encoder(motor_id)
motor_values.append(motor_value)
encoder_readings.append(encoder_value)

# Fit regression model using collected data
regression_model = fit_linear_regression(encoder_readings, motor_values)
save_model(regression_model, f"motor_{motor_id}_regression.pkl")

Notice, for XHand, we do not fit the regression model for all motor. As we found the mapping between exoskeleton joints and robot hand motor are very close to linear. In this case, you can simply change the calibration angles. See video for details. We also provide our mapping for both hand in the repo such that you can directly use it without fitting the regression model. However, you might also need to slighly adjust the regression model. Also see video for details.

## 2. Data Generation & Collection

Collect, process, and prepare training data

#### Data Generation Pipeline

For each collected exoskeleton demonstration, we execute the following data processing pipeline:

# Data Generation Pipeline for DexUMI
for demo_video in exoskeleton_demonstrations:
# Step 0: Synchronize multi-modal data streams
sync_data_sources(wrist_camera, encoder_readings, wrist_pose, tactile_sensor)

# Step 1: Record robot hand video by replaying actions
robot_video = replay_on_robot(encoder_readings)

# Step 2: Resize exoskeleton&robot hand videos

# Step 3: Segment hands from both video streams
exo_mask = segment_exoskeleton(demo_video)
robot_mask = segment_robot_hand(robot_video)

# Step 4: Remove exoskeleton and inpaint background
clean_background = inpaint_video(demo_video, exo_mask)

# Step 5: Composite final high-fidelity manipulation video
final_video = composite_videos(clean_background, robot_video, robot_mask, exo_mask)
save_training_data(final_video, action_labels)

This pipeline transforms raw exoskeleton demonstrations into high-quality training data by removing the human operator and exoskeleton hardware while preserving the nature occlusion between hand and object.

Data generation pipeline overview

Data Generation Commands

cd DexUMI/real_script/data_generation_pipeline
# Sync different data source and replay the exoskelon action on robot hand.
# This cover the Step 0 and Step 1 in the data generation pipeline Pseudocode.
# Modify the DATA_DIR, TARGET_DIR and REFERENCE_DIR before running
./process.sh

# Run data processing pipeline
# This cover the Step 1, 2, 3, 4 and 5 in the data generation pipeline Pseudocode.
# Modify the config/render/render_all_dataset.yaml before running
python render_all_dataset.py

# Generate the final training data
python 6_generate_dataset.py -d path/to/data_replay -t path/to/final_dataset --force-process total --force-adjust

##### Segmentation Setup (finish it before actual data collection/generation)

To achieve automatic segmentation of the exoskeleton and robot hand, you need to configure prompt points before starting data collection and processing. This is a one-time setup process.

Follow these steps to complete the setup:

- Collect Reference Episode: Wear the exoskeleton and collect one initial episode. Ensure your hand and exoskeleton are clearly visible in the first few frames, with the hand in a fully open and comfortable pose. This episode will serve as your reference for all future data collection.
- Generate Robot Replay: Replay the collected episode on the robot hand to create corresponding robot hand video.
- Create Segmentation Prompts: Set up prompt points for both the exoskeleton and robot hand segmentation. Save these prompt points to the reference episode for consistent use across all future collections.

Check the video below for detailed instructions on setting up prompt points and configuring the reference episode.

###### Tips for Better Segmentation Results:

- Color consistency: Wear gloves that match the exoskeleton color to improve detection accuracy
- Prompt point optimization: Experiment with different positive and negative prompt points, as results can vary significantly based on placement
- Sparse prompting: Use fewer, well-placed prompt points rather than dense coverage for better results
- Background exclusion: Place negative prompt points on background regions to prevent SAM2 from including unwanted areas
- Region-based segmentation: Divide the exoskeleton/robot hand into separate regions (thumb, fingers, pinky) with dedicated prompt points for each, then combine masks later

#### Data Collection Guide

We visualiuize the prompt points on the wrist camera image. Make sure to adjust your hand and exoskelton to fully cover the prompt points. We also visualize the current encoder reading on the image. The text become red when the encoder reading is not aligned with the prompt points.

Data Generation Commands

cd DexUMI/real_script/data_collection/
# If you do not have a force sensor installed, simply omit the -ef flag.
# Create REFERENCE_DIR before running
python record_exoskeleton.py -et -ef --fps 45 --reference-dir /path/to/reference_folder --hand_type xhand/inspire --data-dir /path/to/data

## Real-world deployment

Robot setup

#### Calibrate iPhone to EE transformation matrix

Before deploying the policy in the real world, you need to determine the transformation matrix from the iPhone coordinate system to the robot end effector coordinate system. Since the collected data records the pose of the iPhone rather than the actual robot end effector pose, we need to calibrate the transformation matrix so that the iPhone pose can be transformed to the robot end effector pose during deployment. In the following figure, we show two images of 3D printed mounting components between the robot hand and UR5/5e. Mounting component (a) is for actual deployment while mounting component (b) is for calibration. The only difference is that you can place an iPhone on the calibration component. Note that in image (b), the iPhone pose in the robot hand wrist (flange) frame is exactly the same as the iPhone pose in the exoskeleton wrist (flange) frame. Therefore, we can use mounting component (b) to determine how to transfer the iPhone pose to the robot end effector pose.

Robot setup diagram

Inspire Deployment (https://cad.onshape.com/documents/4aa21a6e06eba7dd255c8517/w/a44322658aa13f88f7d08457/) Inspire Calibration (https://cad.onshape.com/documents/9e742a9a2379a725cdc9a562/w/8b5baceda30481d9935c140c/) XHand Deployment (https://cad.onshape.com/documents/356d3078b9f9edebd2b4b479/w/db3bdeefa5b9535e8b2f8dcc/) XHand Calibration (https://cad.onshape.com/documents/bf166d351db6cb561f39a75f/w/f51ca28220c4b9478ad1b8e9/)

In the video, we only calibrate the translation part as we can infer the rotation matrix from definition of the iPhone coordinate frame and UR5/5e end effector coordinate frame. Our script also supports calibrate the rotation matrix. However, in this case, you need to slighly modify the real_script/calibration/record_ur5_trajectory.py to use a space mouse or scripted trajectory to make robot move in SE(3) space (right now is SO(3)).

Calibrate Transformation Matrix between iPhone and robot EE

cd DexUMI/real_script/calibration
# Make UR5 rotate around flange (TCP/Wrist).
# Note: you might need to modify the target_pose on line 60 to place EE in a safe region.
python record_ur5_trajectory.py -rp iphone_calibration

# Run optimization to compute translation part of the matrix
python compute_ur5_iphone_offset.py -rp iphone_calibration

After running the above script, you can set the correct transformation matrix in the eval scripts. You can repeat the above process several time and compute the average transformation matrix to get a more accurate result.

#### Policy Depolyment

Policy Depolyment

cd DexUMI/real_script/eval_policy
region.
python DexUMI/real_script/open_server.py --dexhand --ur5

# open a new terminal
python DexUMI/real_script/eval_policy/eval_xhand.py --model_path path/to/model --ckpt N # for xhand
# or
python DexUMI/real_script/eval_policy/eval_inspire.py --model_path path/to/model --ckpt N # for inspire hand

This page was built using the Academic Project Page Template (https://github.com/eliahuhorwitz/Academic-project-page-template) which was adopted from the Nerfies (https://nerfies.github.io) project page. This website is licensed under a Creative Commons Attribution-ShareAlike 4.0 International License (http://creativecommons.org/licenses/by-sa/4.0/).

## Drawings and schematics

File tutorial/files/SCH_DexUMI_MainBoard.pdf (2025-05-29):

# Power Supply

# STM32F042 Module

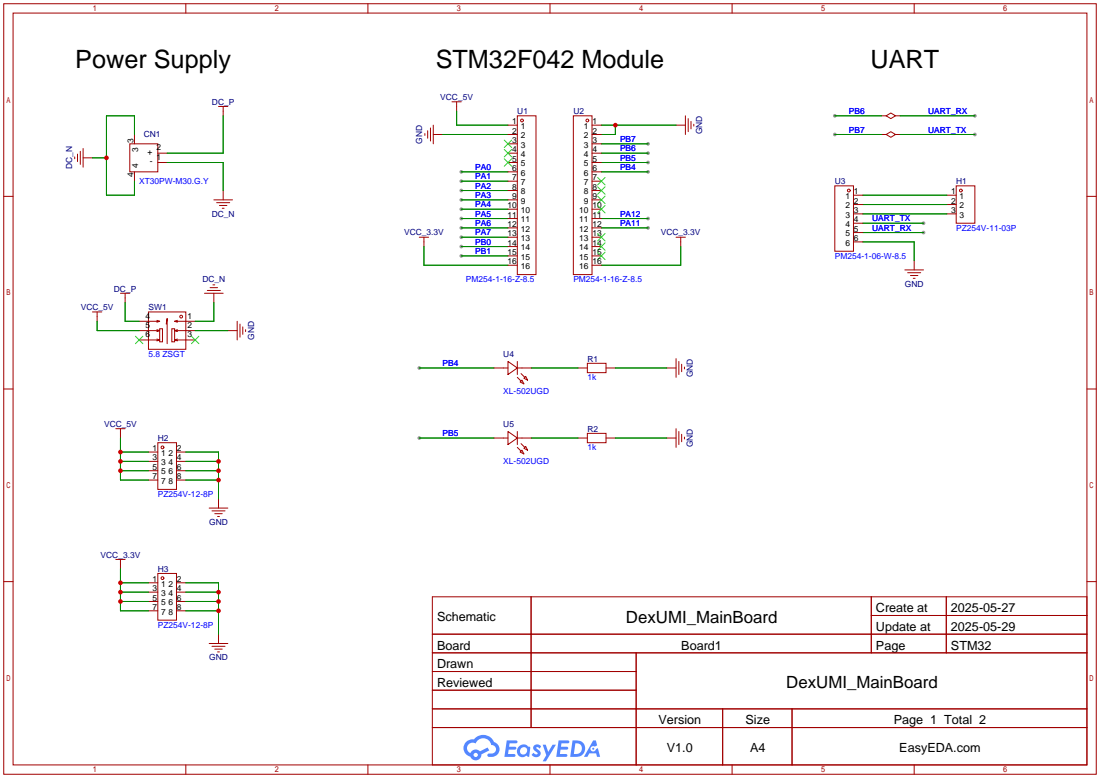
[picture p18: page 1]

Schematic | DexUMI_MainBoard | Create at | 2025-05-27

Update at | 2025-05-29

Board | Board1 | Page | STM32
Drawn | | DexUMI_MainBoard
Reviewed

Version | Size | Page 1 Total 2
V1.0 | A4 | EasyEDA.com

# ADS1256

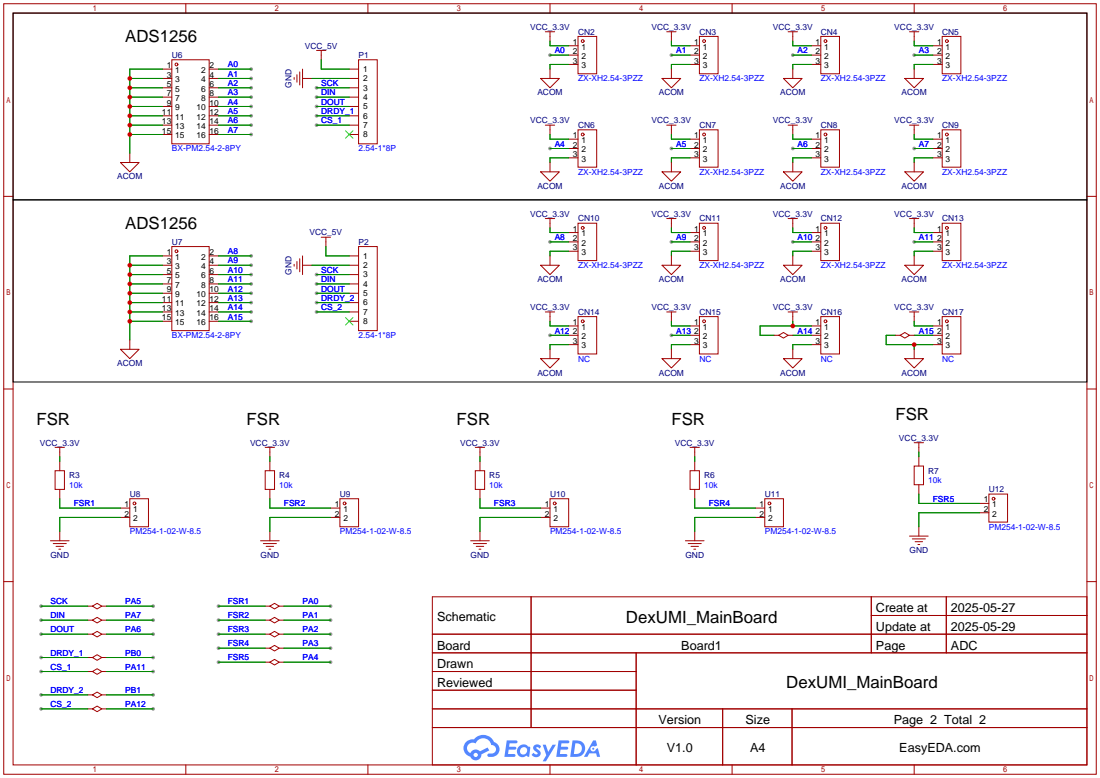
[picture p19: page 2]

Schematic | DexUMI_MainBoard | Create at | 2025-05-27

Update at | 2025-05-29

Board | Board1 | Page | ADC
Drawn | | DexUMI_MainBoard
Reviewed

Version | Size | Page 2 Total 2
V1.0 | A4 | EasyEDA.com

## DC 5.0V + -

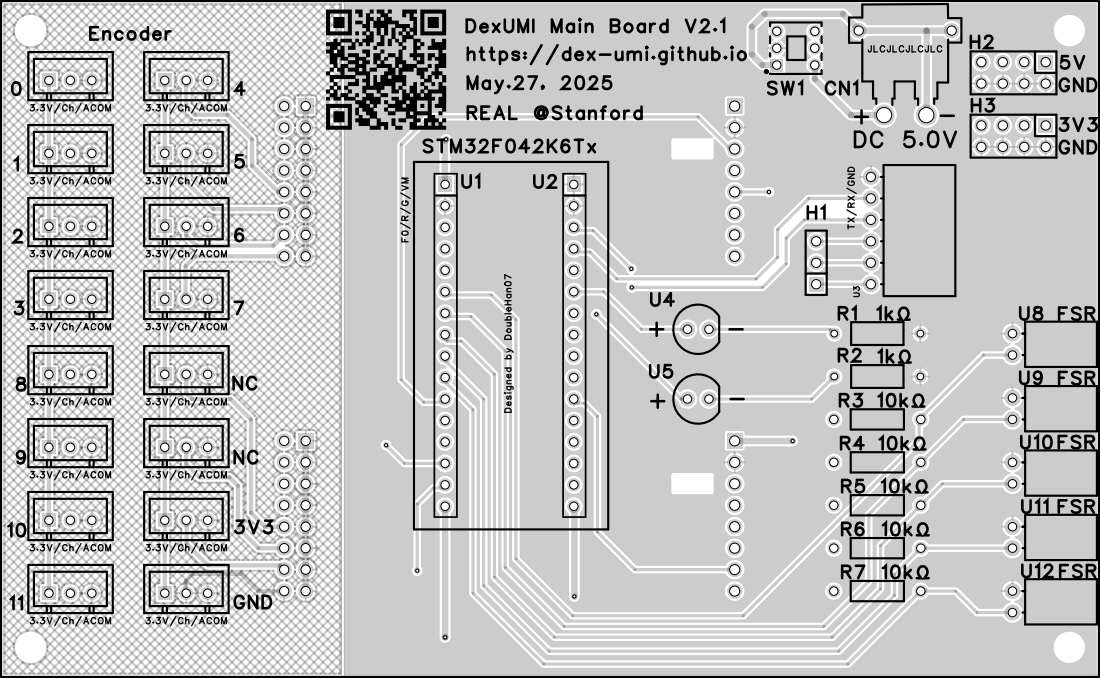
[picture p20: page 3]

DexUMI Main Board V2.1
https://dex-umi.github.io
May.27, 2025

REAL @Stanford Designed by DoubleHan07
STM32F042K6Tx

# ADS1256 P1 P2

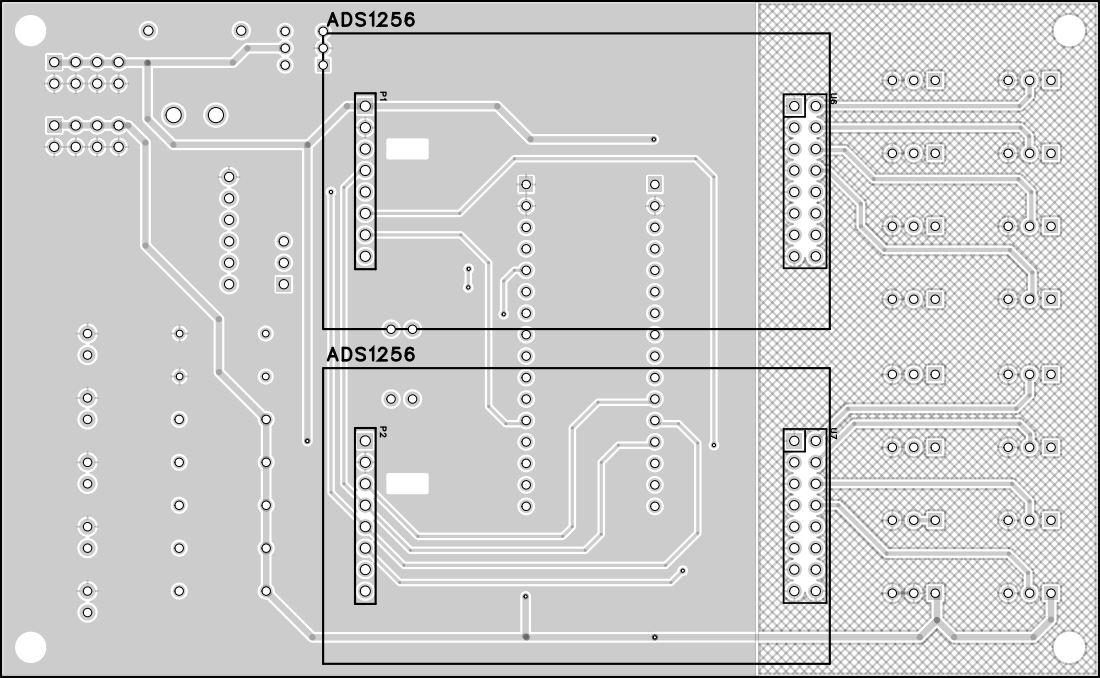
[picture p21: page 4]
ADS1256

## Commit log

2025-05-29 release hardware/deployment Tutorial
    [DexUMI_Inspire.3mf, DexUMI_XHand.3mf]
2025-05-29 rm bom raw
2025-05-29 Update the hardware tutorial.
    [BOM_Board1_DexUMI_MainBoard.xlsx, PickAndPlace_DexUMI_MainBoard.xlsx]
